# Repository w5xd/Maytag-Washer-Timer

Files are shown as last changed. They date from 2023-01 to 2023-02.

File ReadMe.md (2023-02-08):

Maytag LAT8504 Washing machine timer replacement

This repository documents a project that replaces the failed timer on my Maytag washing machine. Maybe there is
enough detail here to duplicate this project, and maybe the parts are even available. There is no particular
reason to use the exact parts I specify here, especially for the relays, but note that K1 and K2 must 
support full motor current, which is specified as 7.5A.

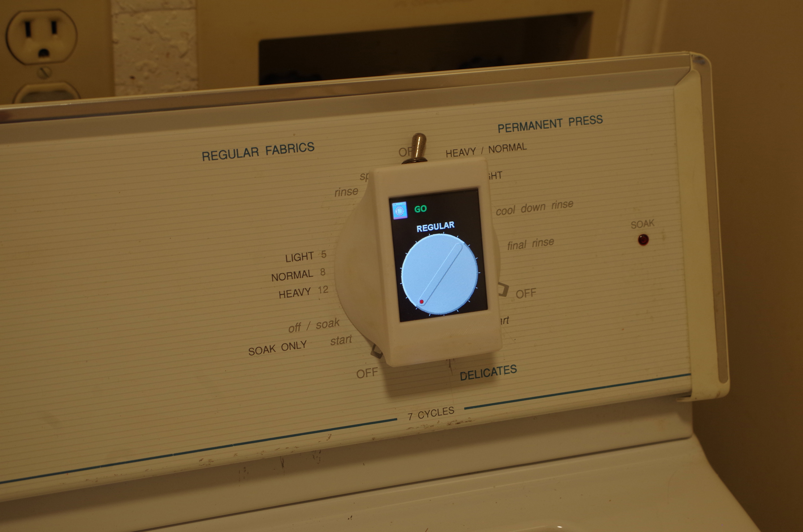
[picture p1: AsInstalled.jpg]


 A few parts, mostly from Sparkfun, can be assembled to replace the timer in the Maytag LAT8504. All these
 parts together cost me less than half the cost of an exact replacement mechanical timer.
 <ul>
 <li> <a href='https://www.sparkfun.com/products/15795'>Qwiic Pro Micro USB-C</a></li>
 <li><a href='https://www.sparkfun.com/products/16566'>Qwiic Quad relay</a> for the qwiic
version of the agitate/spin/soak relay. Or one each of the ANMBEST single and dual 5V coil relays, part ANMBEST_MD314-319 that I 
got off amazon. The later is called "per pin" or "perPin" in the ino and STL. </li>
 <li><a href='https://www.sparkfun.com/products/16833'>Qwiic Quad Solid state relay kit</a></li>
 <li>Two opto isolators are also required, along with a 100K 1/4W resistor for each. A reverse diode is required
 as shown if the opto isolator is unidirectional. Do not omit the 2.7K resistor across 
the opto-isolator LED! It is required to prevent false positive signals to the Arduino for both tub full and
lid closed.
 <li><a href='https://4dsystems.com.au/gen4-ulcd-24pt'>4D systems GEN4-ULCD-24PT</a>
 </ul>

 Four plastic pieces are needed to mount everything. 3D printable STL files are in the stl 
 directory.

 None of the original wires in the washer are cut, nor is the connector for the timer removed. To
 restore the original timer:
<ul><li>The 
 spade lugs at the water temperature switch need to be restored to their original connections
<li>The spade lugs at the water level switch need to be resotred to their original connections (taking
care that the added tap to the Neutral wire is tied down and insulated from connecting to anything.
<li>the 
MOLEX connector for this
 device unplugged
<li> the 3D printed plastic parts around the original timer hole removed
<li> the
 original timer installed and plugged into its original connector. The original connector is
 not plainly visible in the photos below, but its there along with all the wires connected to
 it.
</ul>
The Arduino Pro Micro is soldered to a slightly larger breadboard along with the optoisolators,
 associated resistors, and the 5 pin header for the LCD screen. The circuit diagram is
 here: <a href='Maytag Timer ugrade.pdf'>Maytag Timer ugrade.pdf</a>.

 Photos:
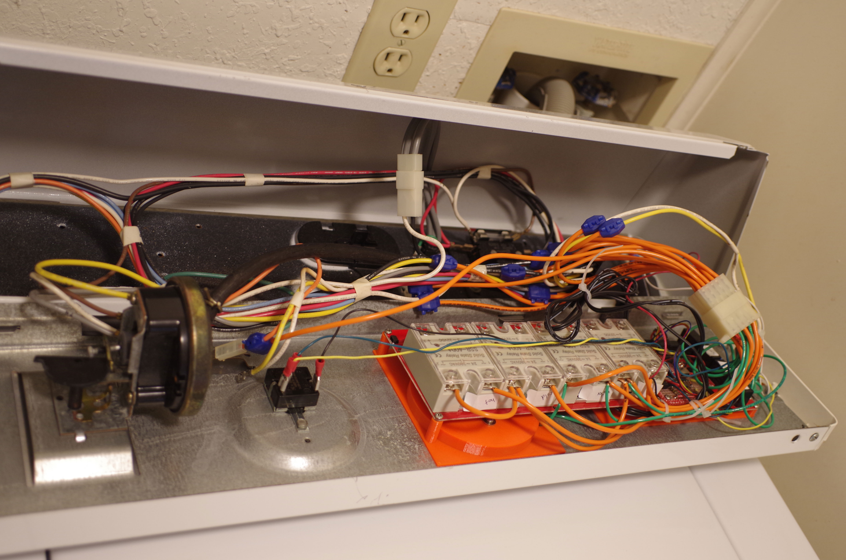
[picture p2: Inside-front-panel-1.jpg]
 
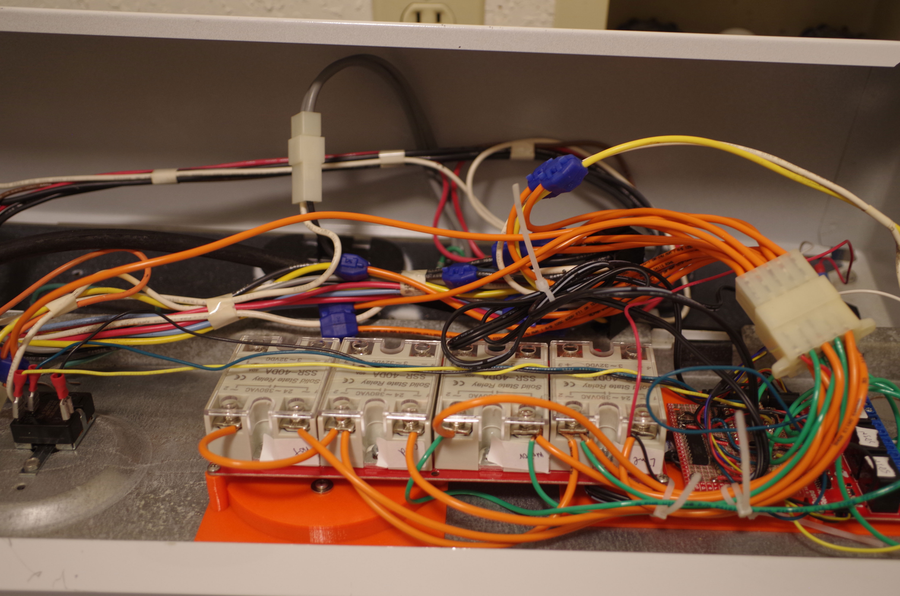
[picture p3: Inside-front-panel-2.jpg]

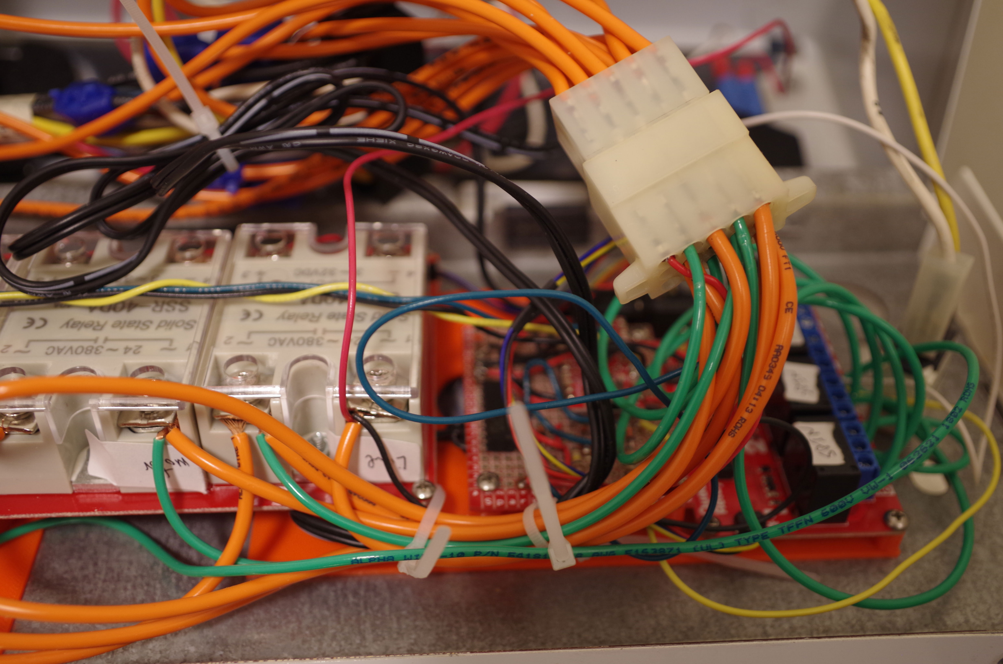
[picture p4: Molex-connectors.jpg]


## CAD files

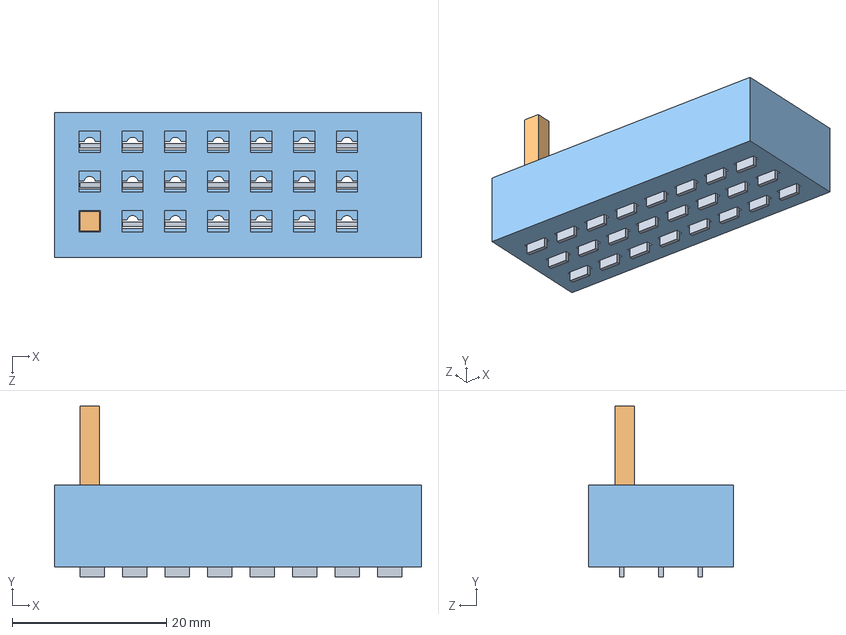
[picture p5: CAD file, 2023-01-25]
CAD/MaytagController.SLDASM
47.6 x 22.1 x 18.9 mm
MaytagSocket
MaytagAdapter

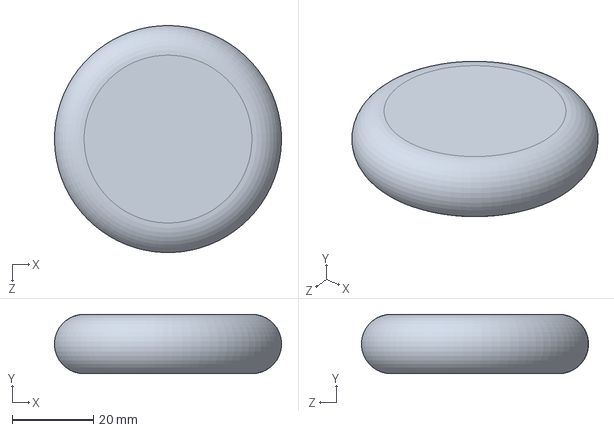
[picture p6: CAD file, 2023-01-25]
CAD/MainKnob.SLDPRT
55.8 x 14.6 x 55.8 mm

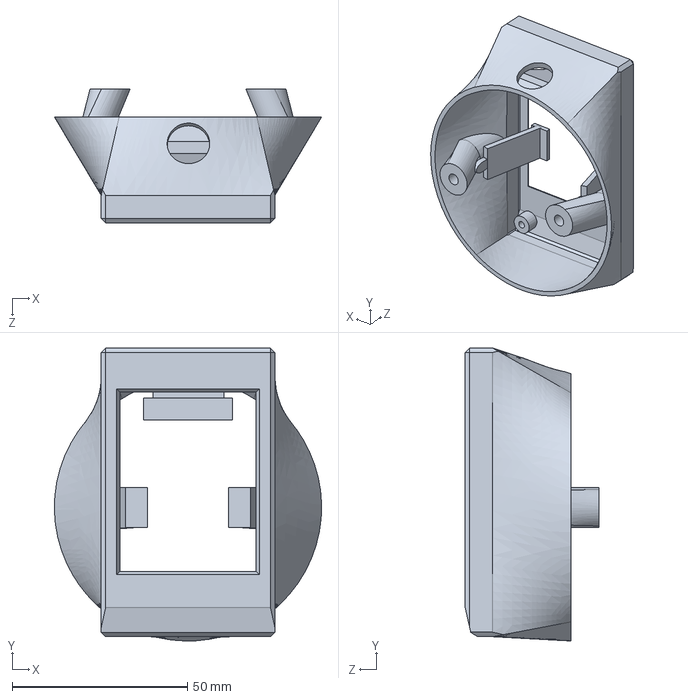
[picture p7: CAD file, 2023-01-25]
CAD/LcdBezel.SLDPRT
76.2 x 83.5 x 38.1 mm

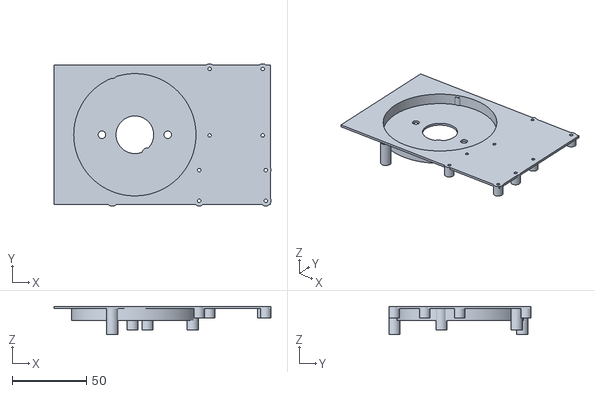
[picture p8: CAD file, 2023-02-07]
stl/PcbMounting-perPin.STL
146.6 x 96.2 x 19.1

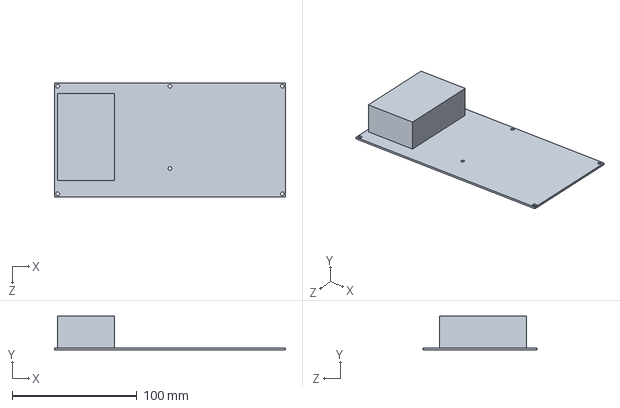
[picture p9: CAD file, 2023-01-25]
CAD/SparkfunQwiicSolidStateRelays.SLDPRT
185.4 x 27.0 x 91.4 mm

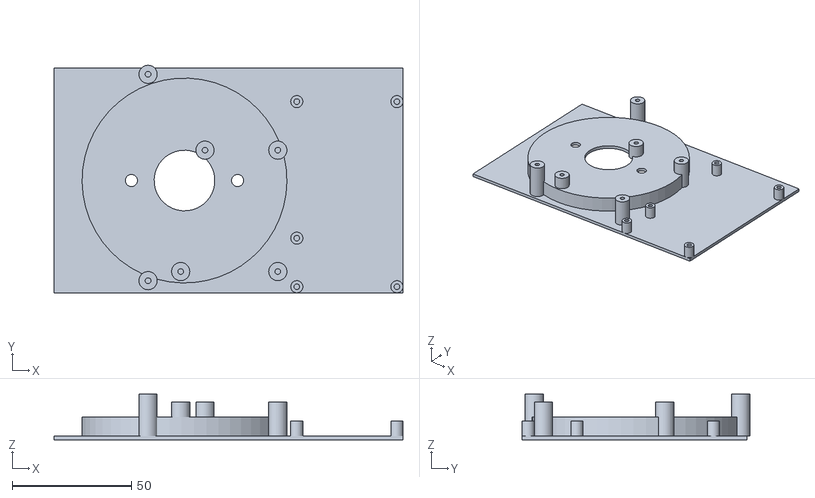
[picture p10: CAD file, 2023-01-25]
stl/PcbMounting-qwiic.STL
146.1 x 95.2 x 19.0

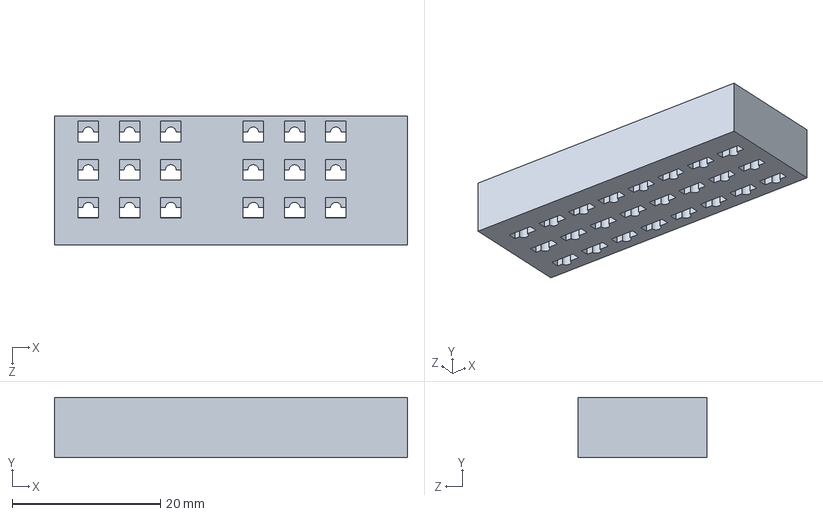
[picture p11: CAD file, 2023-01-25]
CAD/MaytagAdapter.SLDPRT
47.6 x 8.13 x 17.3 mm

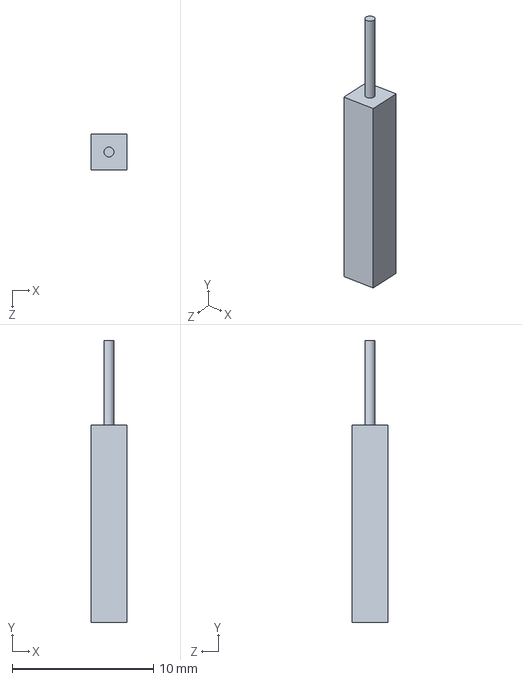
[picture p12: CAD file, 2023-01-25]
CAD/ArduinoPin.SLDPRT
2.52 x 20.0 x 2.52 mm

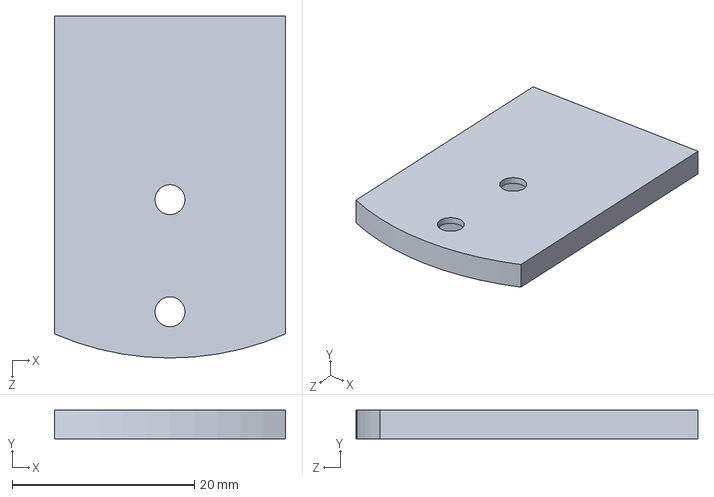
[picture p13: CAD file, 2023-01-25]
CAD/SpareMountNutBracket.SLDPRT
25.4 x 3.17 x 37.6 mm

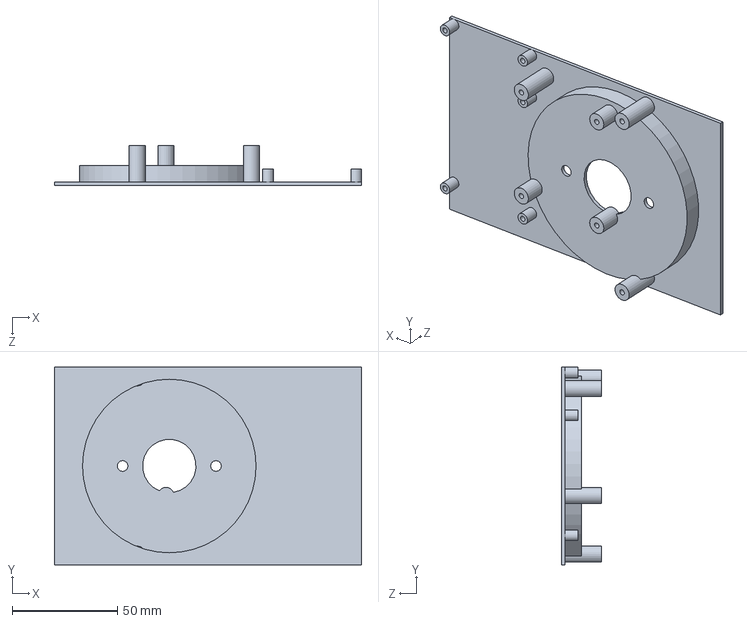
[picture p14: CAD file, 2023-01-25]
CAD/PcbMounting.SLDPRT
146.1 x 94.0 x 19.1 mm

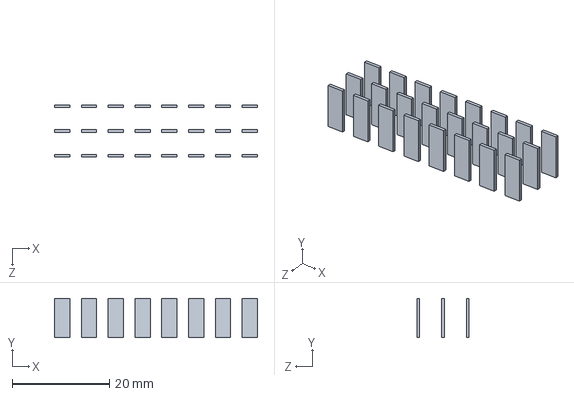
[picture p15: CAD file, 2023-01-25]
CAD/MaytagSocket.SLDPRT
41.8 x 8.13 x 10.7 mm

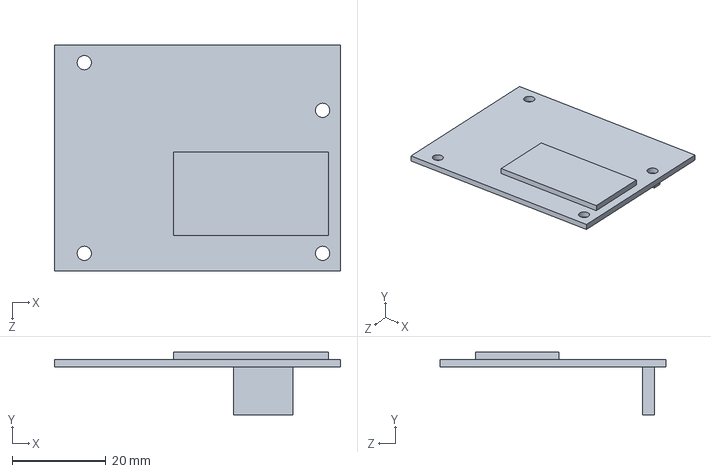
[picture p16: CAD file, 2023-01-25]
CAD/ArduinoPcb.SLDPRT
61.0 x 13.3 x 48.3 mm

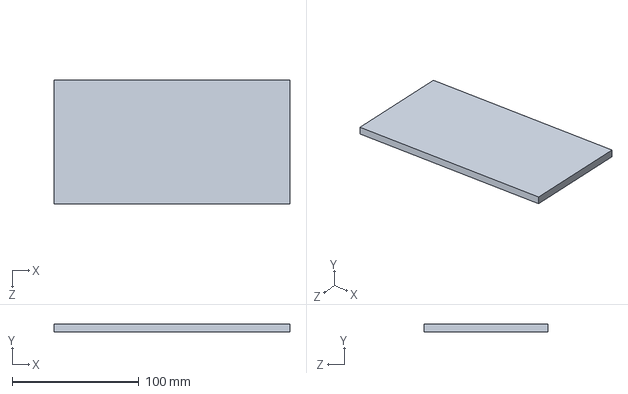
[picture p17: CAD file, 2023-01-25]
CAD/Lid.SLDPRT
185.9 x 6.35 x 97.8 mm

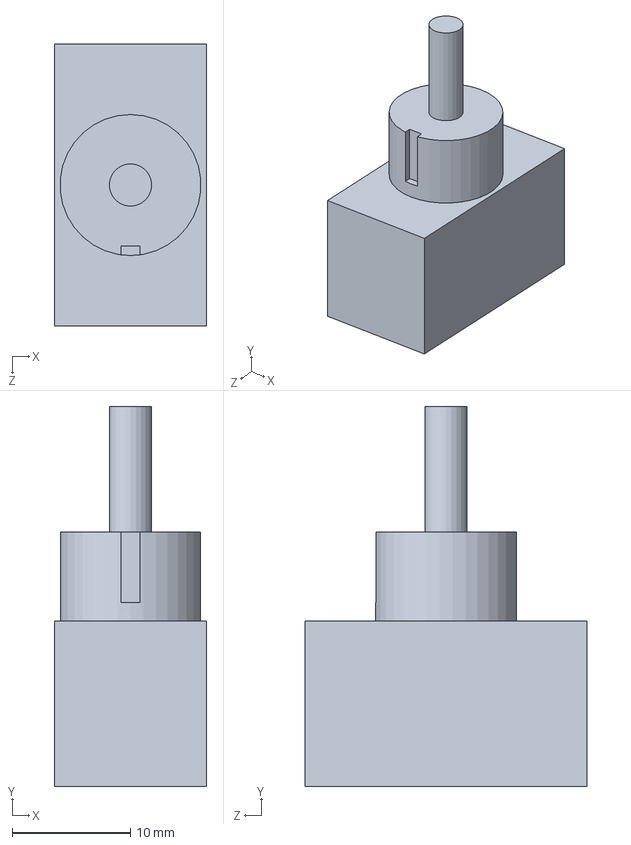
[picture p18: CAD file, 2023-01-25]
CAD/Power Switch.SLDPRT
12.9 x 32.1 x 23.8 mm

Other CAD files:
CAD/SS-Relay-Bracket.SLDPRT
CAD/MaytagFrontPanel.SLDPRT
CAD/SparkFunQwiicQuadRelay.SLDPRT
CAD/LetteringPlate.SLDPRT
stl/LcdBezel.STL
stl/SS-Relay-Bracket.STL
stl/SpareMountNutBracket.STL

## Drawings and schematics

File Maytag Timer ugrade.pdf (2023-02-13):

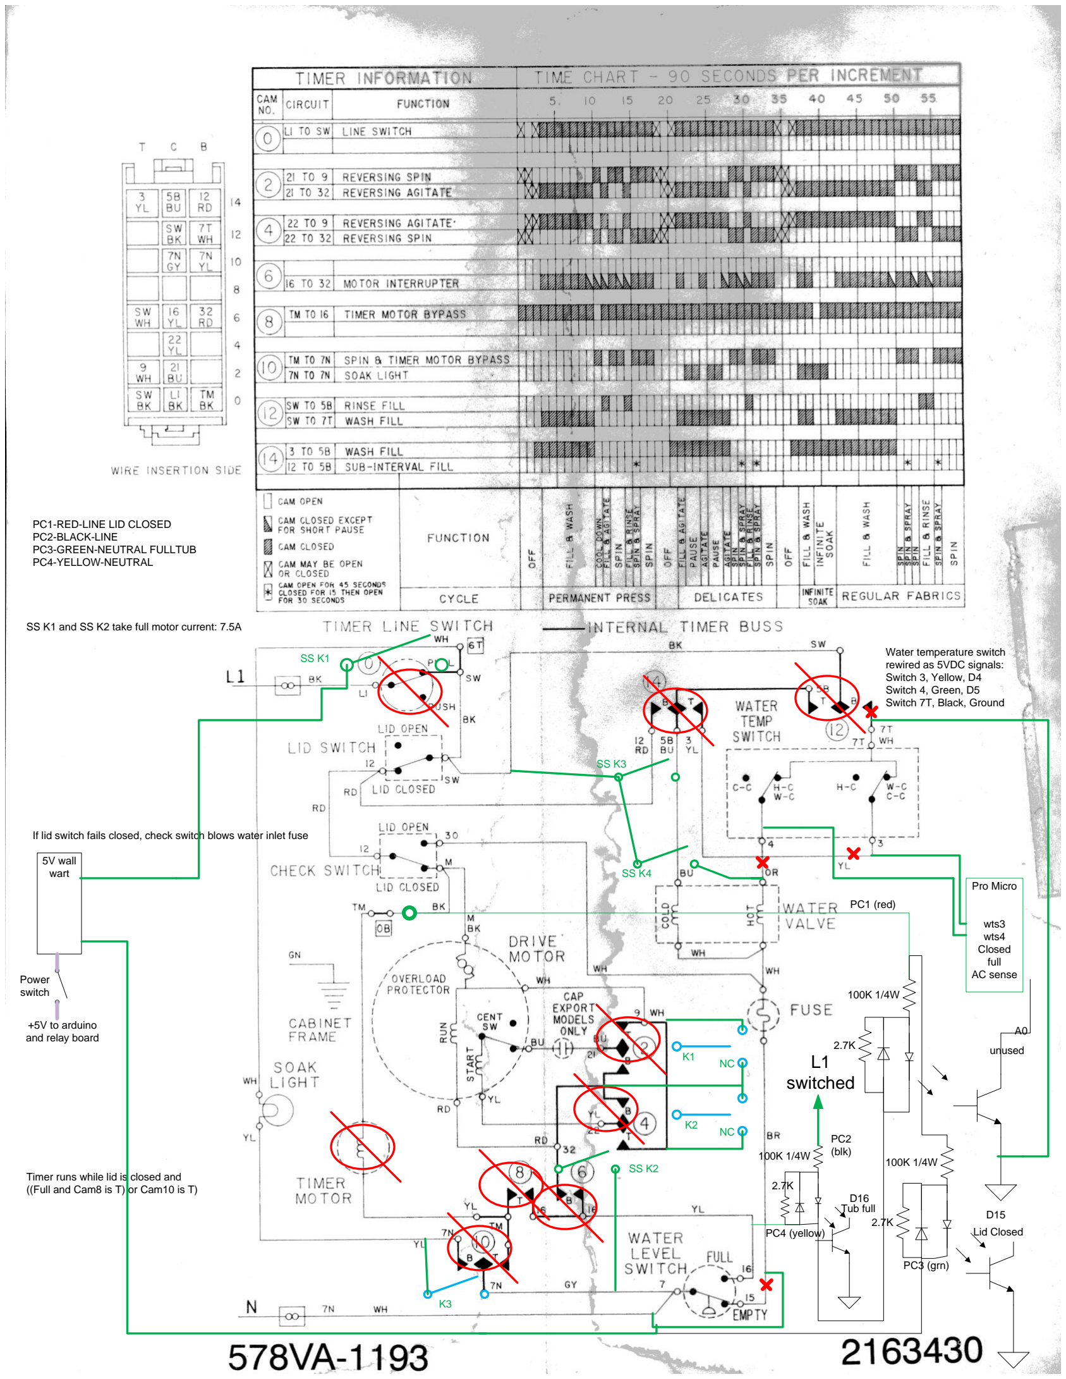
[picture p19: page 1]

SS K1

SS K2

SS K3

SS K4

K3

K2

K1

NC

NC | 100K 1/4W

Pro Micro

wts3 wts4 Closed full AC sense

Timer runs while lid is closed and ((Full and Cam8 is T) or Cam10 is T)

Water temperature switch rewired as 5VDC signals: Switch 3, Yellow, D4 Switch 4, Green, D5 Switch 7T, Black, Ground

unused

Lid Closed 100K 1/4W

If lid switch fails closed, check switch blows water inlet fuse 5V wall wart

+5V to arduino and relay board

PC1-RED-LINE LID CLOSED PC2-BLACK-LINE PC3-GREEN-NEUTRAL FULLTUB PC4-YELLOW-NEUTRAL

PC1 (red)

PC3 (grn) PC4 (yellow) | D15

A0

SS K1 and SS K2 take full motor current: 7.5A

Power switch

Tub full 100K 1/4W PC2 (blk)

D16

L1

# switched

2.7K

2.7K 2.7K

## SS K4 Hot valve Cold valve

yellow | green

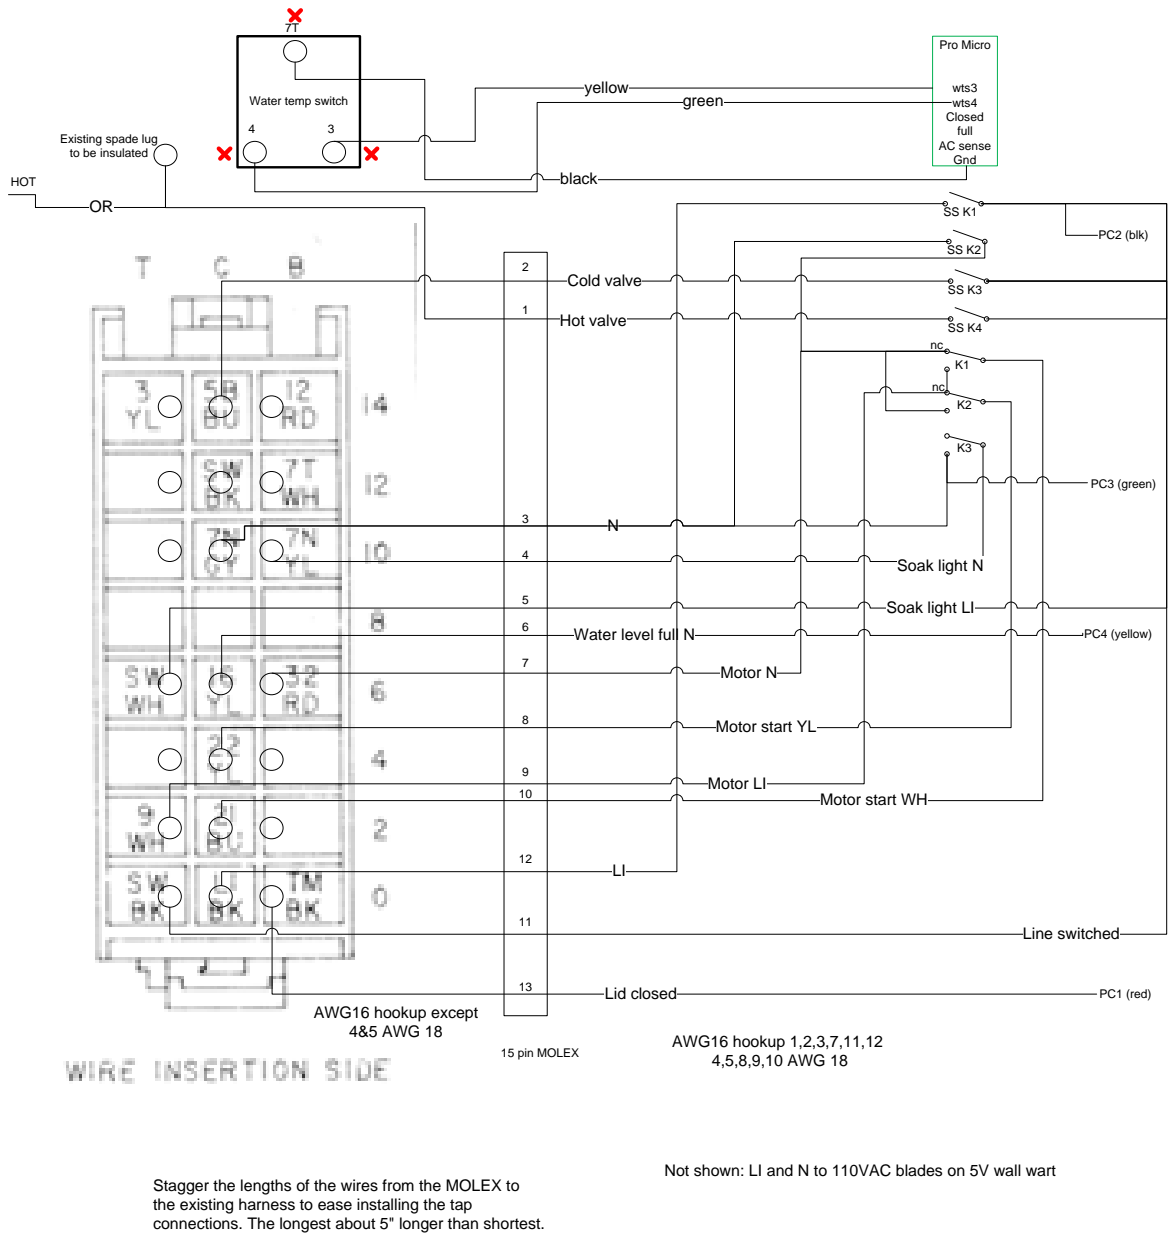
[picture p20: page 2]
15 pin MOLEX; Line switched; Soak light N; Motor N; Motor LI; OR HOT; Water temp switch 4; Pro Micro; PC1 (red); PC2 (blk); PC4 (yellow); PC3 (green); Lid closed; Existing spade lug to be insulated; 13 AWG16 hookup except; 4&5 AWG 18; AWG16 hookup 1,2,3,7,11,12; 4,5,8,9,10 AWG 18

wts3 wts4 Closed full AC sense Gnd black

Soak light LI

Water level full N

Motor start YL

Motor start WH

Not shown: LI and N to 110VAC blades on 5V wall wart

Stagger the lengths of the wires from the MOLEX to the existing harness to ease installing the tap connections. The longest about 5" longer than shortest.

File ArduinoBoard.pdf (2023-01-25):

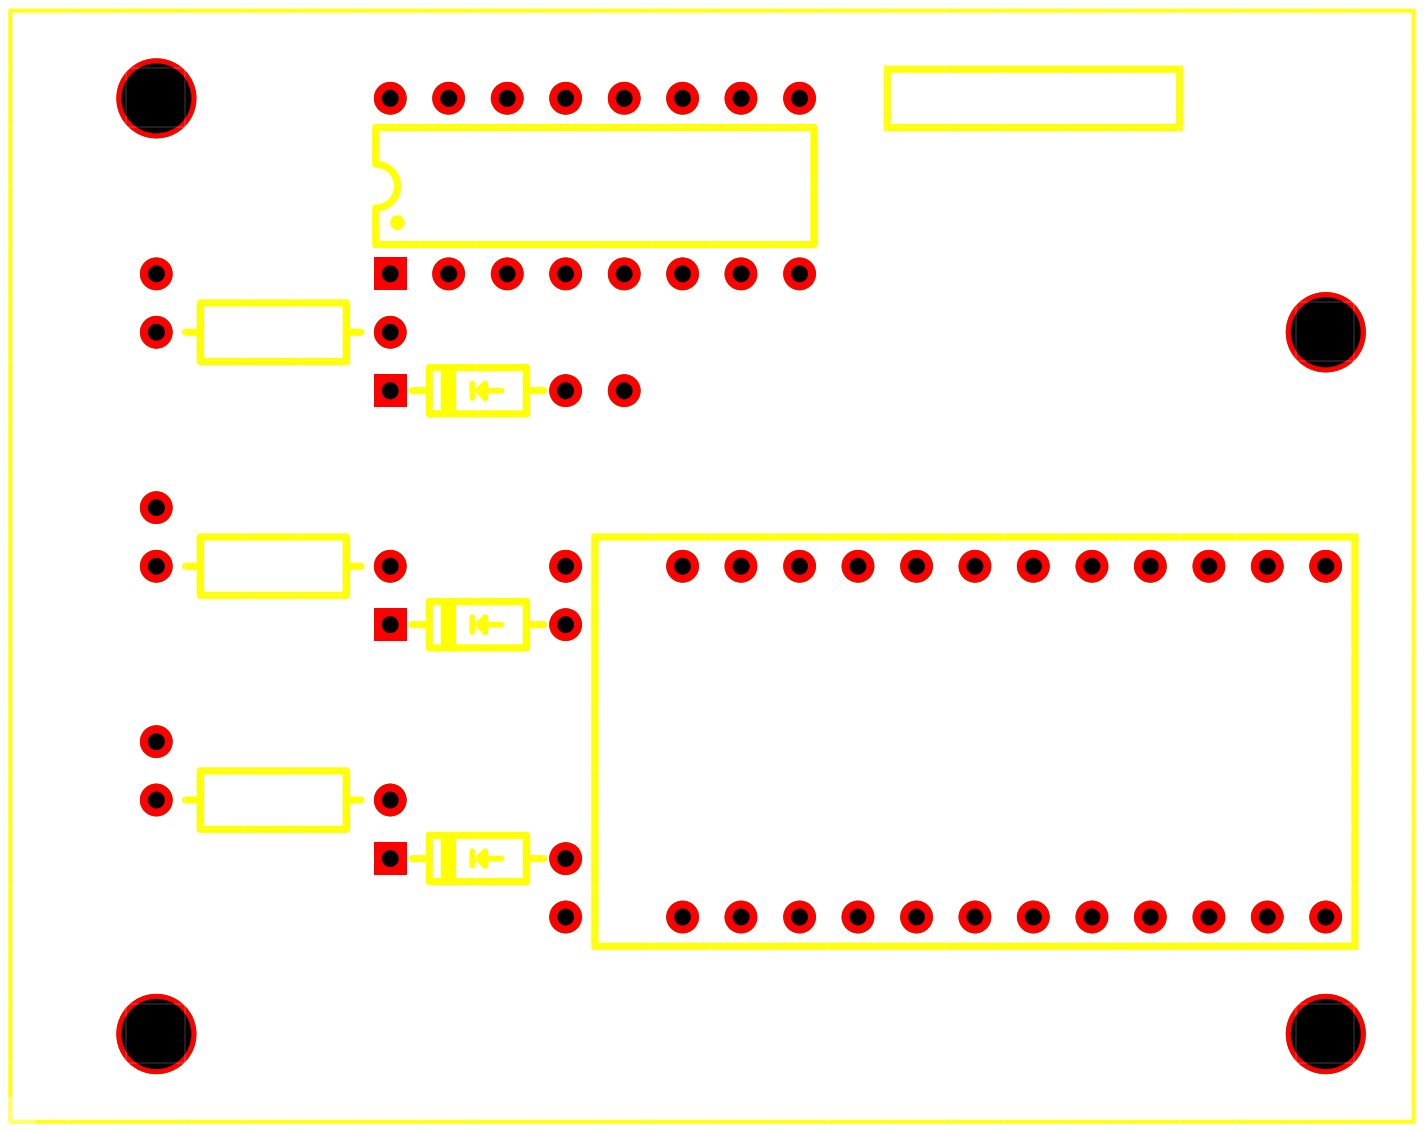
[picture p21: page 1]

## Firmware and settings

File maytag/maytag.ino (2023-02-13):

/* Maytag washer timer implementation.
* This sketch runs on a Sparkfun Pro Micro and matches the behavior of the Maytag mechanical
* timer LAT8504. There are 7 different relay outputs which correspond (roughly) the cams on
* the mechanical timer. There are two input pins that sense the position of two switches
* in the washer: the lid-closed switch and the tub-full switch. The mechanical switches
* retain (most of) their original functions, but this sketch also needs to know their
* positions in order to advance the cycle timer, or wait for something to happen, i.e. for
* the tub to fill, or the lid to close.
*/
// Serial is debug diagnostics on USB
// Serial1 is the gen4-Ulcd-24PT
#include <avr/wdt.h>
#include <SparkFun_Qwiic_Relay.h>
#include <genieArduino.h>
#include "MaytagCycleDefinitions.h"

// I built the first iteration with two qwiic relay boards, but had a failure in one of them
// and found it easier to replace it with discrete relays. The qwiic codes are under
// conditional compile on MECH_RELAY_TYPE
#define MECH_RELAY_TYPE 1 // 0 is qwiic, 1 is digital pin per output

// All these conditional compile directives are 0 for production program
#define INTERACTIVE_DEBUG_MODE 0
#define SIMULATE_LIDandFULL 0

#define DIM(x) (sizeof(x)/sizeof(x[0]))

class RelayPerPin {
    // This class has mostly the same methods as Sparkfun's qwiic relay
    // class for ease in switching this sketch between the two different hardware versions.
public:
    RelayPerPin(int numRelayPins, const int pinsAssigned[])
        : numRelays(numRelayPins)
        , pins(pinsAssigned)
    { }
    int begin() 
    {
        for (int i = 0; i < numRelays; i++)
        {
            digitalWrite(pins[i], LOW);
            pinMode(pins[i], OUTPUT);
        }
        return 1;
    }
    void turnAllRelaysOff()
    {
        for (int i = 0; i < numRelays; i++)
            digitalWrite(pins[i], LOW);
    }
    void turnRelayOff(uint8_t which)
    {
        digitalWrite(pins[which-1], LOW);
    }
    void turnRelayOn(uint8_t which)
    {
        digitalWrite(pins[which-1], HIGH);
    }
private:
    const int numRelays;
    const int *pins;
};

static const int HISTORY_LENGTH = 100;
class NoisyPollinPin {
public:
    NoisyPollinPin(int pin) 
        : pinAssignment(pin)
        , lastUpdate(0)
        , next(0)
        , history({})
    {
    }
    void setup()
    {
        pinMode(pinAssignment, INPUT_PULLUP);
    }
    void update(unsigned long now)
    {
        if (now == lastUpdate)
            return; // at most one sample per msec
        lastUpdate = now;
        history[next++] = digitalRead(pinAssignment) == LOW;
        if (next >= HISTORY_LENGTH)
            next = 0;
    }
    bool value() const
    {
        uint16_t ones(0);
        for (int i = 0; i < HISTORY_LENGTH; i++)
            if (history[i])  ones += 1;
        return ones >= HISTORY_LENGTH / 4;
    }
private:
    bool history[HISTORY_LENGTH];
    uint16_t next;
    unsigned long lastUpdate;
    const int pinAssignment;
};

namespace {
    const uint8_t MECH_RELAY_I2CADDR = 0x6d;
    const uint8_t SS_RELAY_IC2ADDR = 0X8;
    const uint32_t SERIAL_BAUD_RATE = 38400;

    enum SSRelayAssign_t { RLYSS_MAIN_LINE = 1,
        RLYSS_MOTOR = 2,
        RLYSS_COLD_WATER_FILL = 3,
        RLYSS_HOT_WATER_FILL = 4};
    enum MechRelayAssign_t { RLYM_DIRECTION1 = 1,
        RLYM_DIRECTION2 = 2,
        RLYM_SOAKLIGHT = 3};

    const uint8_t PIN_LIDCLOSED_SENSE = 15;        
    const uint8_t PIN_EMPTYFULL_SENSE = 16;    

    const int PIN_RLYM_DIRECTION1 = 6;
    const int PIN_RLYM_DIRECTION2 = 7;
    const int PIN_RLYM_SOAK = 8;

#if INTERACTIVE_DEBUG_MODE==0
    // The Pro Micro has a couple of LEDs that are used by the USB serial, but in this compiled mode, there is no USB
    const int PIN_LID_LED = 30;
    const int PIN_EMPTYFULL_LED = 17;
#endif

    const uint8_t PIN_WATERTEMP3 = 4;
    const uint8_t PIN_WATERTEMP4 = 5;

    const uint8_t PIN_RESETLCD = A3;

    const int MSEC_AC_SENSE_ASSUME_OFF = 100;

    enum {MAIN_KNOB_STOPPED, MAIN_KNOB_RUNNING}
        gMainKnobState = MAIN_KNOB_STOPPED;

    const uint8_t MOTOR_DIRECTION_RELAY_SETTLE_MSEC = 50;

    // The design for the genie display has 17 "settings." This enumeration must match what the genie has
    enum { NUM_GENIE_DISPLAY_CYCLE_SETTINGS = 17, GENIE_DISPLAY_CYCLE_START = 2, GENIE_LOWEST_TIME_IDX = 8 };
    // Those 17 settings correspond rougly to the labeling on the washer's front panel around its original timer.
    const uint16_t UserCycleToTime[NUM_GENIE_DISPLAY_CYCLE_SETTINGS] PROGMEM =
    {    // the genie object starts at angle 180.
        // the dryer display starts at angle 0
        2867, // spin

        3331, // SOAK
        3782, // REGULAR
        3782 + 180, // 9 min
        3782 + 2 * 180, // 6 min
        3782 + 3 * 180, // 3 min
        4766, // rinse
        4955, // spin

        // IDX = 8 = GENIE_LOWEST_TIME_IDX
        268, // PERMANENT PRESS
        268 + 180, // 9 min
        268 + 2 * 180, // 6 min
        268 + 3 * 180, // 3 min
        990, // cool down rinse
        1260, // final rinse
        1350, // spin

        1889, // DELICATES
        2702, // rinse
    };

    enum { INFINITE_SOAK_INDEX = 3, NUM_STOP_TIMES = 5 };
    const uint16_t StopTimes[NUM_STOP_TIMES] =
    {
        0,
        1621,  // Permanent press stops
        3063,    // Delicates stops
        3515, // INFINITE_SOAK_INDEX
        5316, // Regular stops (also is time zero)
    };

    void genieEvents();
    void checkAdvanceTimer(int32_t elapsedMsec, bool advance);
    void applyStateToRelays();
    void checkUpdateLEDcounter(int32_t elapsedMsec);
    void checkUpdateCycleDisplay();
    void checkUpdateMsecToIdx();

#if MECH_RELAY_TYPE==0
    Qwiic_Relay mechRelays(MECH_RELAY_I2CADDR);
#elif MECH_RELAY_TYPE==1
    const int mechRelayPins[] = 
    {   // order must match enum MechRelayAssign_t
        PIN_RLYM_DIRECTION1,
        PIN_RLYM_DIRECTION2,
        PIN_RLYM_SOAK
    };
    RelayPerPin mechRelays(DIM(mechRelayPins), mechRelayPins);
#else
#error "Unknown MECH_RELAY_TYPE"
#endif
    Qwiic_Relay ssRelays(SS_RELAY_IC2ADDR);

    uint16_t gTimerSequenceSeconds = 0; 
    CycleDefinition gCurrentCycleDef;

    Genie genie;
    const int GENIE_USER_BUTTON1_ON_FORM0 = 0;
    const int GENIE_USER_BUTTON2_ON_FORM0 = 1;

    const int GENIE_USER_BUTTON1_ON_FORM1 = 2;
    const int GENIE_USER_BUTTON2_ON_FORM1 = 3;

#if SIMULATE_LIDandFULL != 0
    bool lidClosed = false;
    bool tubFull = false;
#endif

#if INTERACTIVE_DEBUG_MODE
    bool quickTime = false;
#endif

    bool userChangedCycleWhileStopped = true;

    bool lidIsClosed;
    bool tubIsFull;

    NoisyPollinPin lidClosedPin(PIN_LIDCLOSED_SENSE);
    NoisyPollinPin tubFullPin(PIN_EMPTYFULL_SENSE);
}

void setup()
{
#if (INTERACTIVE_DEBUG_MODE)
    delay(5000);    // pro micro usb enumeration takes a long time on Windows 10. give it a chance
    Serial.begin(SERIAL_BAUD_RATE);
    Serial.println("Maytag LAT8504AAE washing machine timer");
#endif

    Wire.begin();
    auto mechStart = mechRelays.begin();
    auto ssStart = ssRelays.begin();
#if (INTERACTIVE_DEBUG_MODE)
    if (!mechStart)
        Serial.println("Mechanical relay i2c init failed!");
    if (!ssStart)
        Serial.println("Solid state relay i2c init failed!");
#endif
    ssRelays.turnAllRelaysOff();
    mechRelays.turnAllRelaysOff();

    // start up genie LCD************************
    Serial1.begin(200000);
    genie.Begin(Serial1);
    genie.AttachEventHandler(genieEvents);
    digitalWrite(PIN_RESETLCD, LOW);
    pinMode(PIN_RESETLCD, OUTPUT);
    delay(100);
    pinMode(PIN_RESETLCD, INPUT);
    delay(3500); // wait for genie
    genie.WriteContrast(10);
    genie.WriteObject(GENIE_OBJ_4DBUTTON, 0, 1);
    genie.WriteObject(GENIE_OBJ_4DBUTTON, 1, 1);
    genie.WriteObject(GENIE_OBJ_ROTARYSW, 0, GENIE_DISPLAY_CYCLE_START);
    genie.WriteObject(GENIE_OBJ_STRINGS, 0, GENIE_DISPLAY_CYCLE_START);

    pinMode(PIN_WATERTEMP3, INPUT_PULLUP);
    pinMode(PIN_WATERTEMP4, INPUT_PULLUP);

#if INTERACTIVE_DEBUG_MODE==0
    pinMode(PIN_LID_LED, OUTPUT);
    pinMode(PIN_EMPTYFULL_LED, OUTPUT);
#endif
    
    lidClosedPin.setup();
    tubFullPin.setup();

    memcpy_P(&gCurrentCycleDef, &MaytagLAT8504[0], sizeof(CycleDefinition));

    // watch dog timer. If this sketch fails to run, then reset the Arduino, which turns off the washing machine.
    wdt_enable(WDTO_8S);
}

void loop()
{
    wdt_reset();
#if (INTERACTIVE_DEBUG_MODE)
    // only when built in this special debug mode do we take input
    while (Serial.available())
    {
        char n = Serial.read();
        if (isalpha(n))
            n = toupper(n);
        switch (n)
        {
#if SIMULATE_LIDandFULL != 0
        case 'L':
            lidClosed = false;
            Serial.println("lid is open");
            break;
        case 'C':
            lidClosed = true;
            Serial.println("lid is closed");
            break;
        case 'F':
            tubFull = true;
            lidClosed = true;
            Serial.println("tub is full");
            break;
        case 'E':
            tubFull = false;
            Serial.println("tub is empty");
            break;
#endif

        case 'Q':
            quickTime = true;
            Serial.println("time is 10x");
            break;
        case 'S':
            quickTime = false;
            Serial.println("time is real time");
        }
    }
#endif

    static unsigned long prevNow;
    unsigned long now = millis();
    int32_t elapsed = now - prevNow;
    prevNow = now;

    genie.DoEvents();
    bool isEnabled = gMainKnobState != MAIN_KNOB_STOPPED;
    if (!isEnabled)
    {
        auto wasOn = ssRelays.getState(RLYSS_MAIN_LINE);
        ssRelays.turnAllRelaysOff(); 
        if (wasOn)
            delay(MOTOR_DIRECTION_RELAY_SETTLE_MSEC); // when turning off, let solid state finish first.
        mechRelays.turnAllRelaysOff(); 
        checkAdvanceTimer(elapsed, false); // keeps the tub full LED up to date.
        // the lid closed LED can't be updated with RLYSS_MAIN_LINE off (see the circuit diagram)
        return;
    }

    checkAdvanceTimer(elapsed, true);
    checkUpdateLEDcounter(elapsed);
    checkUpdateMsecToIdx();
    applyStateToRelays();
}

namespace {
    uint8_t whichCycleStep(uint16_t timerSequenceSeconds)
    {    // binary search the step number from the number of seconds into the timer cycle
        uint8_t lowest = 0;
        uint8_t highest = NUM_WASHER_TIMER_STEPS - 1;
        for (;;)
        {
            uint8_t whichStep = (highest + lowest) >> 1;
            uint16_t stepStartSeconds = pgm_read_word_near(&MaytagLAT8504[whichStep].timeStampSeconds);
            int16_t compare = stepStartSeconds - timerSequenceSeconds;
            if (compare == 0)
                return whichStep;
            else if (compare < 0)
                lowest = whichStep;
            else
                highest = whichStep;
            uint8_t diff = highest - lowest;
            if (diff <= 1)
            {   // down to only two candidates
                stepStartSeconds = pgm_read_word_near(&MaytagLAT8504[highest].timeStampSeconds);
                compare = stepStartSeconds - timerSequenceSeconds;
                if (compare > 0)
                    return lowest;
                else
                    return highest;
            }
        }
    }

    void transitionOffToOn(uint16_t genieObjValue)
    {
        if (userChangedCycleWhileStopped)
        {
            gTimerSequenceSeconds =  pgm_read_word_near(&UserCycleToTime[genieObjValue]);
#if (INTERACTIVE_DEBUG_MODE)
            Serial.print("transitionOffToOn idx=");
            Serial.print(genieObjValue);
            Serial.print(" seconds=");
            Serial.println(gTimerSequenceSeconds);
            Serial.flush();
#endif
        }
        gMainKnobState = MAIN_KNOB_RUNNING;
        ssRelays.turnRelayOn(RLYSS_MAIN_LINE);
        // With RLYSS_MAIN_LINE on, poll the lid closed sensor for 100msec to get its state right.
        auto now = millis();
        while (millis() - now < MSEC_AC_SENSE_ASSUME_OFF)
            checkAdvanceTimer(0,0);
    }

    uint8_t secTogenieIdx(uint16_t secs)
    {    
        if (secs < pgm_read_word_near(&UserCycleToTime[GENIE_LOWEST_TIME_IDX]))
            secs += TIMER_FULL_CYCLE; // modular on TIMER_FULL_CYCLE
        int i = 0;
        for (int j = 0; j < NUM_GENIE_DISPLAY_CYCLE_SETTINGS; j += 1)
        {
            i = GENIE_LOWEST_TIME_IDX - j - 1;
            if (i < 0)
                i += NUM_GENIE_DISPLAY_CYCLE_SETTINGS;
            uint16_t secondsStart = pgm_read_word_near(&UserCycleToTime[i]);
            if (secs >= secondsStart)
                break;
        }
        return i;
    }

    void transitionOnToOff()
    {
        gMainKnobState = MAIN_KNOB_STOPPED;
        userChangedCycleWhileStopped = false;
        // move rotary switch to nearest cycle corresponding to gTimerSequenceSeconds
        int i = secTogenieIdx(gTimerSequenceSeconds);
        genie.WriteObject(GENIE_OBJ_ROTARYSW, 0, i);
#if (INTERACTIVE_DEBUG_MODE)
        Serial.print("transitionOnToOff sec=");
        Serial.print(gTimerSequenceSeconds);
        Serial.print(" idx="); Serial.print(i);
        Serial.println();
        Serial.flush();
#endif
    }

    void genieEvents()
    {
        genieFrame Event;
        if (!genie.DequeueEvent(&Event))
            return;
#if (INTERACTIVE_DEBUG_MODE)
        Serial.print("Event cmd: ");
        Serial.print((int)Event.reportObject.cmd);
        Serial.print(" typ: "); Serial.print((int)Event.reportObject.object);
        Serial.print(" obj: "); Serial.print((int)Event.reportObject.index);
        Serial.print(" val: "); Serial.println((int)Event.reportObject.data_lsb | (int)(Event.reportObject.data_msb << 8));
        Serial.flush();
#endif

        if (genie.EventIs(&Event, GENIE_REPORT_EVENT, GENIE_OBJ_USERBUTTON, GENIE_USER_BUTTON1_ON_FORM0) ||
            genie.EventIs(&Event, GENIE_REPORT_EVENT, GENIE_OBJ_USERBUTTON, GENIE_USER_BUTTON2_ON_FORM0))
        {    // cycle-setting form button pressed
                 genie.ReadObject(GENIE_OBJ_STRINGS, 0);
                genie.WriteObject(GENIE_OBJ_FORM, 1, 1);
        } else if (genie.EventIs(&Event, GENIE_REPORT_EVENT, GENIE_OBJ_USERBUTTON, GENIE_USER_BUTTON1_ON_FORM1) ||
            genie.EventIs(&Event, GENIE_REPORT_EVENT, GENIE_OBJ_USERBUTTON, GENIE_USER_BUTTON2_ON_FORM1))
        {    // in-progress form button pressed
                genie.ReadObject(GENIE_OBJ_STRINGS, 1);
                genie.WriteObject(GENIE_OBJ_FORM, 0, 1);
        } 
        else if (genie.EventIs(&Event, GENIE_REPORT_EVENT, GENIE_OBJ_ROTARYSW, 0))
            userChangedCycleWhileStopped = true;
        else if (genie.EventIs(&Event, GENIE_REPORT_OBJ, GENIE_OBJ_STRINGS, 1))
        {
            transitionOnToOff();
            genie.WriteObject(GENIE_OBJ_STRINGS, 0, genie.GetEventData(&Event));
        } 
        else if (genie.EventIs(&Event, GENIE_REPORT_OBJ, GENIE_OBJ_STRINGS, 0))
        {
            auto newIdx = genie.GetEventData(&Event);
            transitionOffToOn(newIdx);
            genie.WriteObject(GENIE_OBJ_STRINGS, 1, newIdx);
        }
    }

    void checkAdvanceTimer(int32_t elapsedMsec, bool advance)
    {
        static unsigned long lastPollTimestamp;
        static int32_t timerMsec;
        auto now = millis();

#if SIMULATE_LIDandFULL==0
        lidClosedPin.update(now);
        tubFullPin.update(now);
        bool lidClosed = lidIsClosed = lidClosedPin.value();
        bool tubFull = tubIsFull = tubFullPin.value();
#else
        lidIsClosed = lidClosed;
        tubIsFull = tubFull;
#endif

#if (INTERACTIVE_DEBUG_MODE)
        if (quickTime)
            elapsedMsec *= 10;

        static int prevLidClosed = -1;
        if ((int)lidClosed != prevLidClosed)
        {
            Serial.println(lidClosed ? "Lid Closed" : "Lid Open");
            Serial.flush();
        }
        prevLidClosed = (int)lidClosed;

        static int prevTubFull = -1;
        if ((int)tubFull != prevTubFull)
        {
            Serial.println(tubFull ? "Tub Full" : "Tub Empty");
            Serial.flush();
        }
        prevTubFull = (int)tubFull;
#endif
#if INTERACTIVE_DEBUG_MODE==0
        digitalWrite(PIN_LID_LED, lidClosed ? LOW : HIGH);
        digitalWrite(PIN_EMPTYFULL_LED, tubFull ? LOW : HIGH);
#endif

        if (advance)
        {
            if (lidClosed)
            {
                if ((TIMER_ON_CLOSED_LID == gCurrentCycleDef.timerEnableOnClosed) ||
                    (tubFull && (TIMER_ON_FULL == gCurrentCycleDef.timerEnableOnFull)))
                {
                    timerMsec += elapsedMsec;
                    while (timerMsec >= 1000)
                    {
                        gTimerSequenceSeconds += 1;
                        while (gTimerSequenceSeconds >= TIMER_FULL_CYCLE)
                            gTimerSequenceSeconds -= TIMER_FULL_CYCLE;
                        timerMsec -= 1000;
                    }
                }
                else
                    timerMsec = 0;
            }
            else
                timerMsec = 0;
        }
    }

    void applyStateToRelays()
    {
        uint8_t step = whichCycleStep(gTimerSequenceSeconds);
#if (INTERACTIVE_DEBUG_MODE)
        static uint8_t prevStep = -1;
        if (step != prevStep)
        {
            Serial.print("Moving to step idx="); Serial.print(step);
            Serial.print(" at seconds: "); Serial.println(gTimerSequenceSeconds);
            Serial.flush();
        }
        prevStep = step;
#endif
        memcpy_P(&gCurrentCycleDef, &MaytagLAT8504[step], sizeof(CycleDefinition));
        // don't command the direction control relay while the motor relay is on.
        bool motorWasOff = ssRelays.getState(RLYSS_MOTOR) == 0;
        // motorOn is CAM6 combined with either the water level, or CAM8+CAM10
        bool motorOn = (gCurrentCycleDef.motorEnable == MOTOR_ON)  &&
            (tubIsFull || 
                (gCurrentCycleDef.timerEnableOnFull == TIMER_ON_FULL &&
                 gCurrentCycleDef.timerEnableOnClosed == TIMER_ON_CLOSED_LID));
        if (!motorOn)
        {
            ssRelays.turnRelayOff(RLYSS_MOTOR);
            if (!motorWasOff)
                delay(MOTOR_DIRECTION_RELAY_SETTLE_MSEC);
            mechRelays.turnRelayOff(RLYM_DIRECTION1);
            mechRelays.turnRelayOff(RLYM_DIRECTION2);
        }
        else
        {
            if (motorWasOff)
            {
#if (INTERACTIVE_DEBUG_MODE)
                Serial.print("Turning motor on "); 
                Serial.println(gCurrentCycleDef.dir == CAM_AGITATE ? "agitate" : "spin");
                Serial.flush();
#endif
                // the RLYM_DIRECTION relays are commanded in concert
                if (gCurrentCycleDef.dir == CAM_AGITATE)
                {
                    mechRelays.turnRelayOff(RLYM_DIRECTION1);
                    mechRelays.turnRelayOff(RLYM_DIRECTION2);
                }
                else
                {
                    mechRelays.turnRelayOn(RLYM_DIRECTION1);
                    mechRelays.turnRelayOn(RLYM_DIRECTION2);
                }
                delay(MOTOR_DIRECTION_RELAY_SETTLE_MSEC);
            }
            ssRelays.turnRelayOn(RLYSS_MOTOR);
        }

        if (gCurrentCycleDef.soakLight == SOAK_LIGHT)
            mechRelays.turnRelayOn(RLYM_SOAKLIGHT);
        else
            mechRelays.turnRelayOff(RLYM_SOAKLIGHT);

        int pinTemp3 = digitalRead(PIN_WATERTEMP3);
        int pinTemp4 = digitalRead(PIN_WATERTEMP4);

        // cold and hot equations are derived from inspection of the circuit diagram.
        bool cold = ((gCurrentCycleDef.coldWaterCam == TEMPERATURE_CAM_BOTTOM) && lidIsClosed) ||
            (gCurrentCycleDef.coldWaterCam == TEMPERATURE_CAM_OFF && 
                gCurrentCycleDef.hotWaterCam == TEMPERATURE_CAM_TOP) ||
            (gCurrentCycleDef.coldWaterCam == TEMPERATURE_CAM_TOP && pinTemp3 == LOW);
        bool hot = (pinTemp4 == LOW) && (gCurrentCycleDef.hotWaterCam == TEMPERATURE_CAM_BOTTOM);
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

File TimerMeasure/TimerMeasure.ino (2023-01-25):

// This sketch runs on a Mega (or something with at least 21 input pins)
// It uses pin input/output mode changes to probe whether the middle pin in a group of 3 consectutive
// pins is connected to the other two (one lower number, one higher number).
// Each group of 3 is to follow one cam on an oldstyle washing machine timer.
// Every second, it prings to Serial1 what each CAM appears to be (0 is unconnected, T is top, B is bottom and E is both)

enum CamState_t {
    CAM_OFF, CAM_T, CAM_B, CAM_ERROR, NUM_CAM_STATES
};

namespace {
    const int PinCam2T = 53;
    const int PinCam2Pole = 52;
    const int PinCam2B = 51;

    const int PinCam6B = PinCam2B - 6;
    const int PinCam4B = PinCam2B - 3;

    const int NUM_CAMS = 7;

    const char Decode[NUM_CAM_STATES] = { '0', 'T', 'B', 'E' };

    const int CamNumber[NUM_CAMS] = { 2, 4, 6, 8, 10, 12, 14 };

    CamState_t CamStates[NUM_CAMS];

    CamState_t CamLastState[NUM_CAMS];

    int TimesInLastState[NUM_CAMS];
}

void AquireCam(int which)
{
    int pinT = PinCam2T - (3 * which);
    int pinPole = pinT - 1;
    int pinB = pinPole - 1;

    // the maytag timer has internal connections for Cam2 bottom and Cam4 bottom
    // that don't appear on the connector per the pattern of the other cams.
    if (pinB == PinCam2B)
        pinB = PinCam6B;
    else if (pinB == PinCam4B)
        pinB = PinCam6B;

    pinMode(pinPole, OUTPUT);
    pinMode(pinT, INPUT_PULLUP);
    pinMode(pinB, INPUT_PULLUP);
    digitalWrite(pinPole, LOW);

    CamState_t st = CAM_OFF;
    bool pinTValue = digitalRead(pinT) != LOW;
    bool pinBValue = digitalRead(pinB) != LOW;

    if (!pinTValue && !pinBValue)
        st = CAM_ERROR;
    else if (!pinTValue)
        st = CAM_T;
    else if (!pinBValue)
        st = CAM_B;

    if (CamLastState[which] == st)
    {
        TimesInLastState[which] += 1;
        if (TimesInLastState[which] > 4)
            CamStates[which] = st;
    }
    else
    {
        TimesInLastState[which] = 0;
        CamLastState[which] = st;
    }

    // restore the changed pin modes. 
    // This is crucial. Each measurement in this routine depends on the fact
    // that all the other pins not being measured are open circuit (INPUT)
    pinMode(pinPole, INPUT);
    pinMode(pinT, INPUT);
    pinMode(pinB, INPUT);
}


void setup()
{
    Serial1.begin(38400);
    // all pins are left as INPUT except for in AquireCam.
}

void loop()
{
    static long secondsAtLastReport;
    // every loop, acquire all 6 cams
    for (int i = 0; i < NUM_CAMS; i++)
        AquireCam(i);

    long nowSeconds = millis();
    nowSeconds /= 1000;

    if (nowSeconds != secondsAtLastReport)
    {
        secondsAtLastReport = nowSeconds;

        Serial1.print("time ");
        Serial1.print(nowSeconds);
        
        for (int i = 0; i < NUM_CAMS; i++)
        {
            Serial1.print(" Cam");
            Serial1.print(CamNumber[i]);
            Serial1.print(":");
            Serial1.print(Decode[static_cast<int>(CamStates[i])]);
        }
        Serial1.println();
    }


}

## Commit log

2023-02-07 noise suppession resistance
    [Front Panel.cfg, PcbMounting-perPin.STL, PcbMounting-qwiic.STL]
2023-02-09 reverse the empty-full logic
    [maytag.ino]
2023-02-13 tub full is the way the circuit works reliably
